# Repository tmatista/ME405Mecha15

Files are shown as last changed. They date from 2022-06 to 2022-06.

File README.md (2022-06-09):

# ME 405 Mechatronics Pen Plotter Landing Page
#### Authors: Tim Matista, Jason Hu
#### Under the Guidance of: Professor Charlie Refvem, Cal Poly SLO
#### Date: 06/04/2022

## The Pen Plotter Project Definition
#### The Pen Plotter project was devised to allow teams to create a robotic drawing machine in any creative was possible. The requirements for this project were to create a 2-and-a-half degree of freedom robot that, when fed raw HPGL files, draws out shapes using any means necessary. The term "draw" was free to be interpreted in whatever manner we choose. The two main degrees of freedom are as well free to be chosen to be any motion EXCEPT the cartesian coordinate system. The remaining half degree of freedom is used as an actuator, or pen-up pen-down motion. 
#### All devices also must be able to be ran using benchtop power supplies in the laboratory and include a "Bell and Whistle" to uniquely define this project from any similar project done before. 

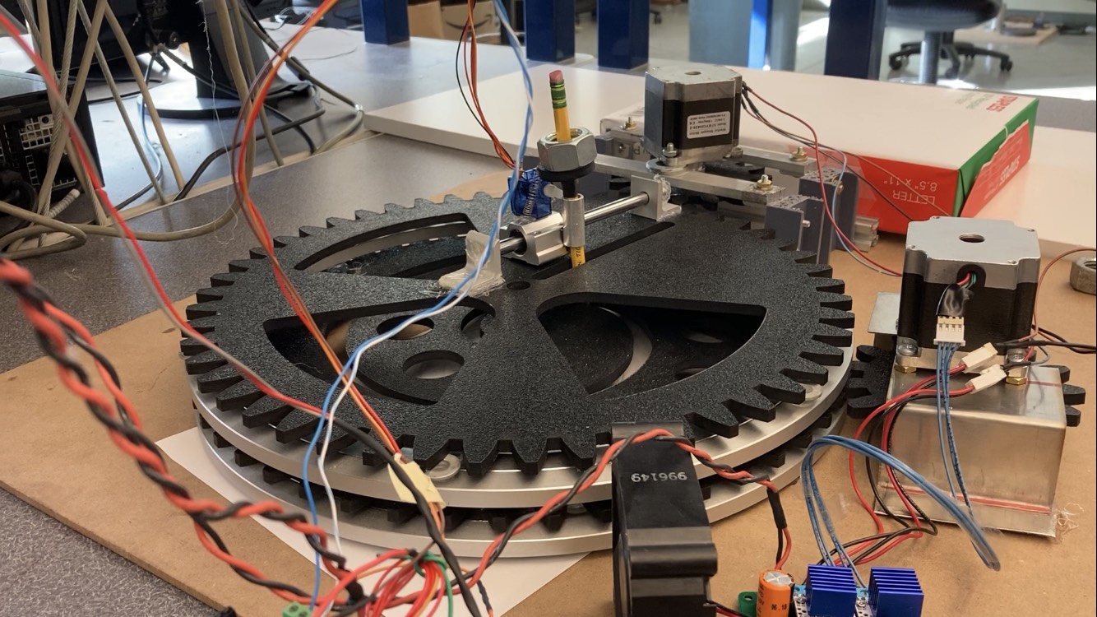
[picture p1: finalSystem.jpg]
Image of assembled System


## Features
#### Our pen plotter design offers a large workspace and the radial symmetry of the system lends itself well to geometric patterened drawings. The pen plotter can raise and lower the pen to allow fo seperate shapes to be drawn. (WHAT ELSE ARE FEATURES?)

## Bell-and-Whistle: Live Plotting
#### The additional feature added to our system is a live plotting system that uses UART to communicate drawing progress from the Nucleo to the computer. This requires a cable to be connected to the STLink in addition to the one plugged into the Shoe of Brian. To set up the live plotting, type "pip install panda" into the command prompt to download the necessary software. Then, run the plotting file by seelcting the appropriate directory and then commanding "python uart_draw.py". A window should open and display the curent pathing of the pen plotter. (INSERT VIDEO OF UART (already uploaded) WHEN THIS IS A "PAGES")

## Operation (WE NEED A WIRING DIAGRAM FOR EVERYTING, INCLUDING SERVO AND ALL THAT)
#### To run the systme, start by saving a drawing as "simple.hpgl" to the Nucleo. Next, move the motors so that the gears are **not** meshed with the disks. This is important because the motors automatically move to their "home" position which may not be what you expect it to be. Next, ensure that the pen is in the raised position. If it isn't this can be manually adjusted by running the "simple.py". Slide a piece of paper under the disks, switch on both power supplies and soft reboot the Nucleo by pressing ctrl+D. The code will report when it has finished parsing your drawing into usable code and the motors may start moving to their home location. When all of this has finished, move the gears into place to mesh with the disks, and press any key to coninue.

#### (INSERT VIDEO OF SYSTEM RUNNING WHEN THIS IS A "PAGES")

## Mecha15's Mechanical Design
#### Team Mecha15 decided to pursue a robot similar to mechanism 94 in the book, "507 Mechanical Movements". The proposed mechanism can be found here: http://507movements.com/mm_094.html
 
### The Discs
#### The proposed mechanism 94 operates using two discs, so we laser cut two discs out of HDPE that were donated by the Robotics Club at Cal Poly. The discs can be separated into a radial disc and a spiral disc. Both gears were cut to have a diameter of 14". 
### Spiral Disc
#### The spiral disc was laser cut out of HDPE at 1/4" thickness, it was designed to have an Archimedes spiral cut into it along with a 50 gear teeth on the outer diameter. Three triangular weight-saving shapes were cut into the spiral disc to cut down on inertial load and allow the user to view drawings below.
### Radial Disc
#### The radial disc was cut with a 4.75" radial slot in it to facilitate movement. This slot starts 0.75" away from the exact center of the disc. Circular weight-saving cuts were made in the radial disc to ease inertial load and allow the user to view drawings below. This disc is outfitted with a linear rail along its radial slot to help facilitate the motion of the pen as well as keep it upright. 
### Lazy Susans
#### Two 14" Lazy Susans (LS) were purchased from Amazon at about 17$/each. These LS are mounted between both discs to facilitate the independent movement of the discs. The discs were secured to the LS using hot glue. The LS can be found on Amazon here: https://www.amazon.com/dp/B07PW63B3Q/ref=twister_B09ZTWL4NN?_encoding=UTF8&th=1
### CAD
#### The Solidworks file used in the design of this project are included in this repository. The files corresponding to the disks and pinion gears were used to laser cut the respective parts.

#### (AT SOME POINT ADD THE JYPTER FILES AND ALL THAT KIND OF STUFF)

## The Motors
### Steppers
#### Two Wantai NEMA 23 motors were chosen for the final design, as these motors are able to produce the torque needed to move both discs independently. These motors are configures in 4-wire bi-polar stepper movement and have 200 counts-per-revolution. These motors are mounted on brackets to elevate them to the desired height. Pinion gears with 15 teeth are attached to the output shafts of the motor and are designed to mesh with the radial and spiral discs gear teeth. 
### Servo
#### A single TowerPro hobby servo motor was selected to control the pen actuation. The motor was dissected and altered for manual control of the internal DC motor and potentiometer. The resistance of the potentiometer changes as the motor spins, and the reistsnace changes the reading of an ADC on the Nucleo. The servo is outfitted with a single cam on its output shaft that physically moves a pen up and down. All of this together allows the Nucleo to sense if the pen has successfuly been raised or lowered.

## The Drivers
#### Both NEMA 23 motors are driven using TMC4210 and TMC2208 driver chips. These chips were selected due to their SPI protocol and silentstepper modes of movement. These chips, along with a capacitor and header pins, were soldered to a prototyping board supplied by Charlie. This board then interfaces with the Shoe-Of-Brian mounted beneath the STM32 Nucleo Microcontroller. An exact pin-out description is as follows: 

| Motor Driver| Nucleo |
|---|---|
| EN1 | C3 |
| EN2 | C2 |
| CLK | C7 | 
| nCS1 | C0 |
| nCS2 | C4 |
| SCK | B3 |
| MOSI | MOSI2 |
| MISO | MISO2 |

## Firmware
#### The software used to impliment the robot was written in Python, for its under-the-hood libaries make calculations, matrix operations and motor movement fairly easy. The software is split up into (??6??) files: (CHECK THIS NUMBER, ADD DESCRIPTIONS FOR ALL)
#### main.py
#### task_motor.py
#### newtonraphson.py
#### tmc4210driver.py
#### filereader.py
#### ihm04a1Driver.py
#### task_share.py
#### cotask.py

### filereader.py
#### This file takes in a raw .hpgl file, parses it, then saves each X, Y, and command coordinate to a .txt file. The command coordinate is simply either a 0 or a 1 corresponding to pen up/pen down respectively. This is done by seperating the .hpgl file at every semicolon, denoting different operations, and then by commas, denoting x and y coordinates. This file will also determine if the distance between two points is greater than a set threshold and interpolates between points as needed. This file will also determine if the requested point is within the workspace that the plotter can reach and adjust points if they are not possible to draw. This file runs as a pre-processing procedure before the coooperative multitasking begins.

### tmc4210driver.py
#### This file is used to instantiate the TMC4210 chip for motor control. It also defines any methods that are used by the task_motor file such as SPI.send_recv, bytearray decoders, or bytearray translators. This allows us to communicate with the chips and access all of the associated functionality. (EXPLAIN WHAT THE METHODS ACTUALLY DO)

### ihm04a1Driver.py
#### (Explain what this does)

### task_motor.py
#### This file initiates each motor object by sending the correct byte arrays to their respective registers, setting the values of P_MUL, P_DIV, A_MAX, pulse_div, and ramp_div. A table containing these parameters is listed below. To briefly summarize, the constants we selected were chosen because of the high inertia of our mechanical system. The relatively low acceleration, for example, ensures that the motors have enough torque to spin without skipping steps. These values were calculated using (INSERT EXCEL HERE) and there is more information about them there as well. 
|  Variable  | Value |
|---|---|
| A_MAX | 80 |
| pulse_div  | 10 |
| ramp_div | 8 |
| P_MUL | 156 |
| P_DIV | 3 |

### newtonraphson.py
#### The Newton Raphson file uses the Newton Raphson method of finding the roots of a non-linear equation to converge on values of theta for the motors. This is how we calculate the inverse kinematics for the system, letting us find the appropriate motor locations to move the pen to a target point.Hand calculations of the Newton Raphson process are attached below.

( Image of assembled System ) (CHANGE THIS TO MATCH IMAGE NAMES FOR HAND CALCS)

### main.py
#### The main file is responsible for scheduling and instantiating the tasks that run all the files described above. We opted with a round-robin scheduling instead of a priority scheduling technique to make sure each task had the opportunity to run. The scheduling for the running of each task is outlined in the table below. The motor task sends the desired position to each motor and them checks if the motors have reached that position. Note that the equation_task and theta_task run at the same period and priority. This would nomrally be a problem, but only one of these tasks can run at a time. These tasks are in chage of determining desired motor positions from either a .hpgl or from a mathmatical pattern, respecitvely. The pud_driver task is in chage fof raising and lowering the pen throughout the drawing process.

| Task Name |  Period (ms) | Priority |
| --- | --- | --- |
| motor_task | 75 | 0 |
| theta_task | 75 | 1 |
| equation_task | 75 | 1 |
| pud_driver | 50 | 2 |

## Difficulties
### Software
#### Many issues faced while coding this project can be attributed to an error found in the creation of the serial bus used to communicate with the TMC4210 chips. The baudrate of this connection was mistakenly set as 100,000 rather than 1,000,000. Once this issue was addressed, the motors worked much more consistantly.
### Hardware(FILL IN THE BLANKS HERE)
#### This project was fraught with hardware difficulties, most stemming from the motors used for the project. Firstly, the provided (part number) motors did not have the torque required to spin the lazy susan bearings. These motors were replaced with (part number) NEMA (number) stepper motors from the Cal Poly Robotics Club. Unfortunately, one of these replacement motors has a shorting problem when the wires are moved. With much difficulty, this has successfuly been mitigated.

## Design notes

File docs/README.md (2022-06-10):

# ME 405 Mechatronics Pen Plotter Landing Page
#### Authors: Tim Matista, Jason Hu
#### Under the Guidance of: Professor Charlie Refvem, Cal Poly SLO
#### Date: 06/04/2022

## The Pen Plotter Project Definition
#### The Pen Plotter project was devised to allow teams to create a robotic drawing machine in any creative was possible. The requirements for this project were to create a 2-and-a-half degree of freedom robot that, when fed raw HPGL files, draws out shapes using any means necessary. The term "draw" was free to be interpreted in whatever manner we choose. The two main degrees of freedom are as well free to be chosen to be any motion EXCEPT the cartesian coordinate system. The remaining half degree of freedom is used as an actuator, or pen-up pen-down motion. 
#### All devices also must be able to be ran using benchtop power supplies in the laboratory and include a "Bell and Whistle" to uniquely define this project from any similar project done before. 

Image of assembled System

## Features
#### Our pen plotter design offers a large workspace and the radial symmetry of the system lends itself well to geometric patterened drawings. The pen plotter can raise and lower the pen to allow fo seperate shapes to be drawn.

## Bell-and-Whistle: Live Plotting
#### The additional feature added to our system is a live plotting system that uses UART to communicate drawing progress from the Nucleo to the computer. This requires a cable to be connected to the STLink in addition to the one plugged into the Shoe of Brian. To set up the live plotting, type "pip install panda" into the command prompt to download the necessary software. Then, run the plotting file by seelcting the appropriate directory and then commanding "python uart_draw.py". A window should open and display the curent pathing of the pen plotter. 

(http://www.youtube.com/watch?v=P3Ct4gNFd5c)

## Operation
#### To run the systme, start by saving a drawing as "simple.hpgl" to the Nucleo. Next, move the motors so that the gears are **not** meshed with the disks. This is important because the motors automatically move to their "home" position which may not be what you expect it to be. Next, ensure that the pen is in the raised position. If it isn't this can be manually adjusted by running the "simple.py". Slide a piece of paper under the disks, switch on both power supplies and soft reboot the Nucleo by pressing ctrl+D. The code will report when it has finished parsing your drawing into usable code and the motors may start moving to their home location. When all of this has finished, move the gears into place to mesh with the disks, and press any key to coninue.

(http://www.youtube.com/watch?v=kh2zqIlsFNg)

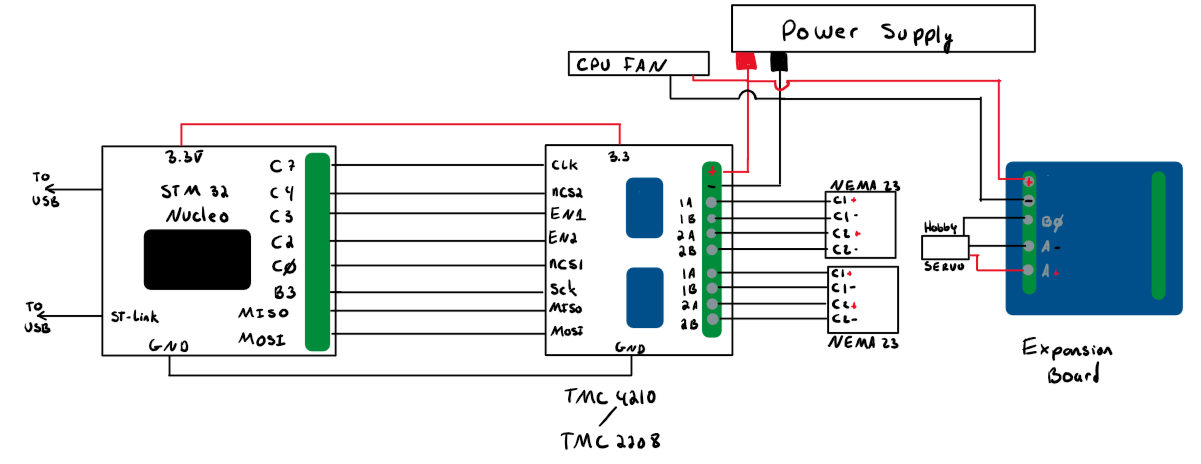
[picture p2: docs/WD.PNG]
Wiring Diagram

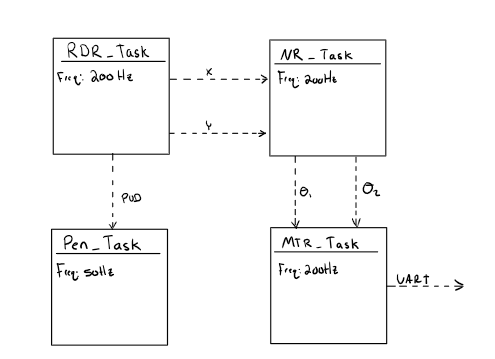
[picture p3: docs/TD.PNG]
High-Level Task Diagram


## Mecha15's Mechanical Design
#### Team Mecha15 decided to pursue a robot similar to mechanism 94 in the book, "507 Mechanical Movements". The proposed mechanism can be found here: http://507movements.com/mm_094.html
### The Discs
#### The proposed mechanism 94 operates using two discs, so we laser cut two discs out of HDPE that were donated by the Robotics Club at Cal Poly. The discs can be separated into a radial disc and a spiral disc. Both gears were cut to have a diameter of 14". 
### Spiral Disc
#### The spiral disc was laser cut out of HDPE at 1/4" thickness, it was designed to have an Archimedes spiral cut into it along with a 50 gear teeth on the outer diameter. Three triangular weight-saving shapes were cut into the spiral disc to cut down on inertial load and allow the user to view drawings below.
### Radial Disc
#### The radial disc was cut with a 4.75" radial slot in it to facilitate movement. This slot starts 0.75" away from the exact center of the disc. Circular weight-saving cuts were made in the radial disc to ease inertial load and allow the user to view drawings below. This disc is outfitted with a linear rail along its radial slot to help facilitate the motion of the pen as well as keep it upright. 
### Lazy Susans
#### Two 14" Lazy Susans (LS) were purchased from Amazon at about 17$/each. These LS are mounted between both discs to facilitate the independent movement of the discs. The discs were secured to the LS using hot glue. The LS can be found on Amazon here: https://www.amazon.com/dp/B07PW63B3Q/ref=twister_B09ZTWL4NN?_encoding=UTF8&th=1
### CAD
#### The Solidworks file used in the design of this project are included in this repository. The files corresponding to the disks and pinion gears were used to laser cut the respective parts.

## The Motors
### Steppers
#### Two Wantai NEMA 23 motors were chosen for the final design, as these motors are able to produce the torque needed to move both discs independently. These motors are configures in 4-wire bi-polar stepper movement and have 200 counts-per-revolution. These motors are mounted on brackets to elevate them to the desired height. Pinion gears with 15 teeth are attached to the output shafts of the motor and are designed to mesh with the radial and spiral discs gear teeth. 
### Servo
#### A single TowerPro hobby servo motor was selected to control the pen actuation. The motor was dissected and altered for manual control of the internal DC motor and potentiometer. The resistance of the potentiometer changes as the motor spins, and the reistsnace changes the reading of an ADC on the Nucleo. The servo is outfitted with a single cam on its output shaft that physically moves a pen up and down. All of this together allows the Nucleo to sense if the pen has successfuly been raised or lowered.

## The Drivers
#### Both NEMA 23 motors are driven using TMC4210 and TMC2208 driver chips. These chips were selected due to their SPI protocol and silentstepper modes of movement. These chips, along with a capacitor and header pins, were soldered to a prototyping board supplied by Charlie. This board then interfaces with the Shoe-Of-Brian mounted beneath the STM32 Nucleo Microcontroller. An exact pin-out description is as follows: 

| Motor Driver| Nucleo |
|---|---|
| EN1 | C3 |
| EN2 | C2 |
| CLK | C7 | 
| nCS1 | C0 |
| nCS2 | C4 |
| SCK | B3 |
| MOSI | MOSI2 |
| MISO | MISO2 |

## Firmware
#### The software used to impliment the robot was written in Python, for its under-the-hood libaries make calculations, matrix operations and motor movement fairly easy. The software is split up into 10 files:
#### main.py
#### task_motor.py
#### newtonraphson.py
#### tmc4210driver.py
#### filereader.py
#### ihm04a1Driver.py
#### uart_draw.py
#### uarter.py
#### task_share.py
#### cotask.py

### main.py
#### The main file is responsible for scheduling and instantiating the tasks that run all the files described above. We opted with a round-robin scheduling instead of a priority scheduling technique to make sure each task had the opportunity to run. The scheduling for the running of each task is outlined in the table below. The motor task sends the desired position to each motor and them checks if the motors have reached that position. Note that the equation_task and theta_task run at the same period and priority. This would nomrally be a problem, but only one of these tasks can run at a time. These tasks are in chage of determining desired motor positions from either a .hpgl or from a mathmatical pattern, respecitvely. The pud_driver task is in chage fof raising and lowering the pen throughout the drawing process.

| Task Name |  Period (ms) | Priority |
| --- | --- | --- |
| motor_task | 75 | 0 |
| theta_task | 75 | 1 |
| equation_task | 75 | 1 |
| pud_driver | 50 | 2 |

### filereader.py
#### This file takes in a raw .hpgl file, parses it, then saves each X, Y, and command coordinate to a .txt file. The command coordinate is simply either a 0 or a 1 corresponding to pen up/pen down respectively. This is done by seperating the .hpgl file at every semicolon, denoting different operations, and then by commas, denoting x and y coordinates. This file will also determine if the distance between two points is greater than a set threshold and interpolates between points as needed. This file will also determine if the requested point is within the workspace that the plotter can reach and adjust points if they are not possible to draw. This file runs as a pre-processing procedure before the coooperative multitasking begins.

### task_motor.py
#### This file initiates each motor object by sending the correct byte arrays to their respective registers, setting the values of P_MUL, P_DIV, A_MAX, pulse_div, and ramp_div. A table containing these parameters is listed below. To briefly summarize, the constants we selected were chosen because of the high inertia of our mechanical system. The relatively low acceleration, for example, ensures that the motors have enough torque to spin without skipping steps. These values were calculated using the linked Excel sheet by Trinamic and there is more information about them there as well. https://www.trinamic.com/fileadmin/assets/Products/ICs_Documents/tmc429_ramp_setup.xls

|  Variable  | Value |
|---|---|
| A_MAX | 80 |
| pulse_div  | 10 |
| ramp_div | 8 |
| P_MUL | 156 |
| P_DIV | 3 |

### newtonraphson.py
#### The Newton Raphson file uses the Newton Raphson method of finding the roots of a non-linear equation to converge on values of theta for the motors. This is how we calculate the inverse kinematics for the system, letting us find the appropriate motor locations to move the pen to a target point. Hand calculations of the Newton Raphson process are attached below, as well as a gif of a simulated drawing in action.

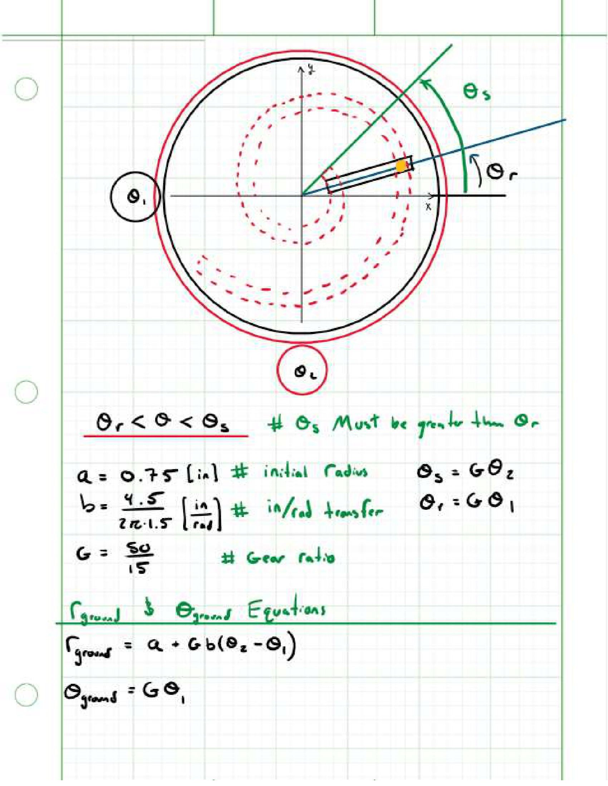
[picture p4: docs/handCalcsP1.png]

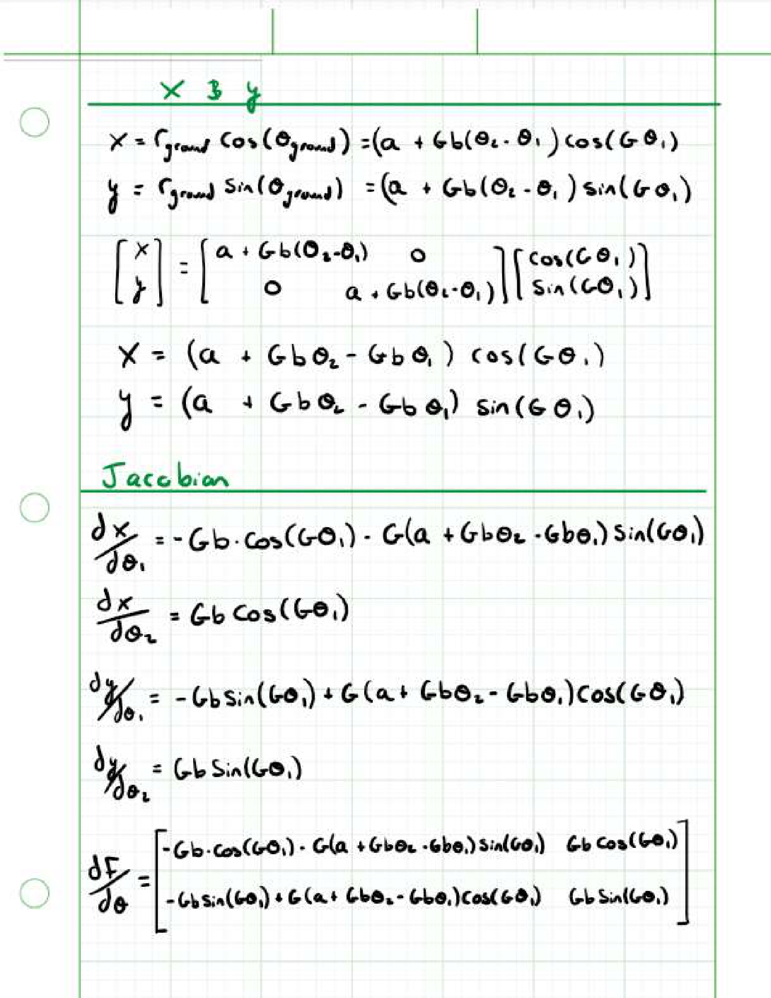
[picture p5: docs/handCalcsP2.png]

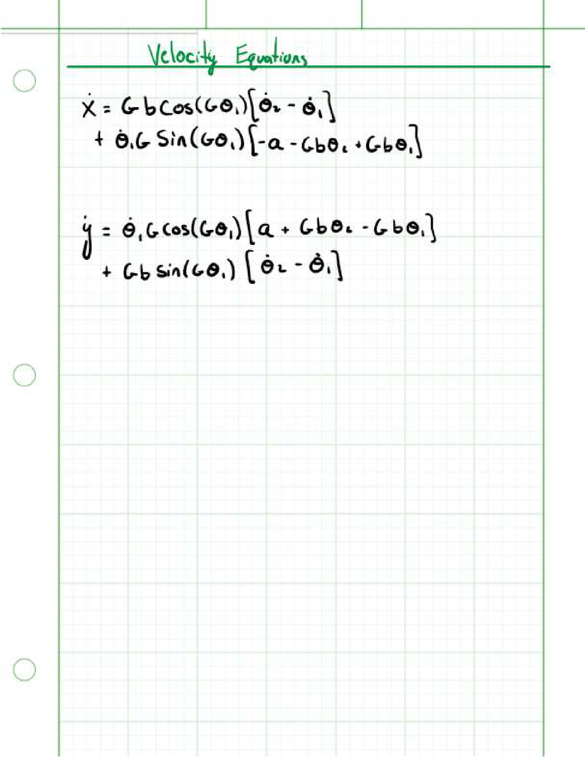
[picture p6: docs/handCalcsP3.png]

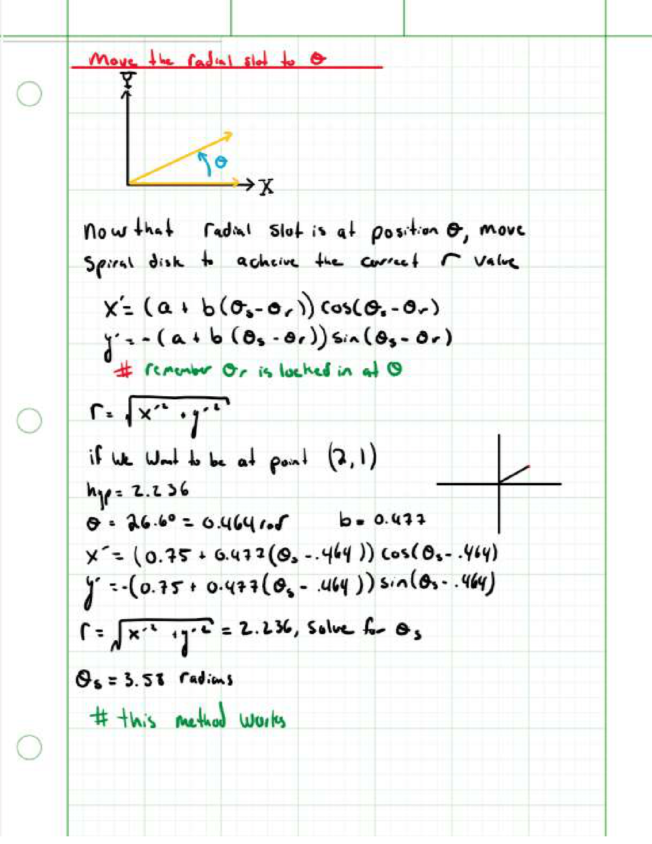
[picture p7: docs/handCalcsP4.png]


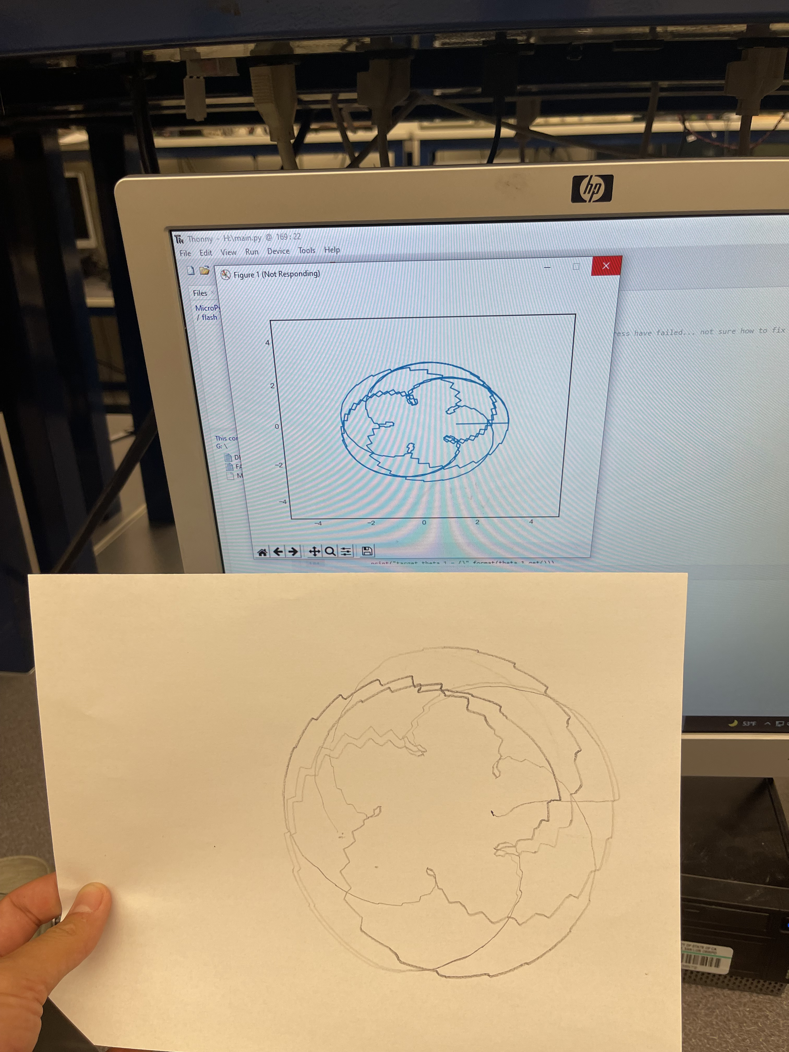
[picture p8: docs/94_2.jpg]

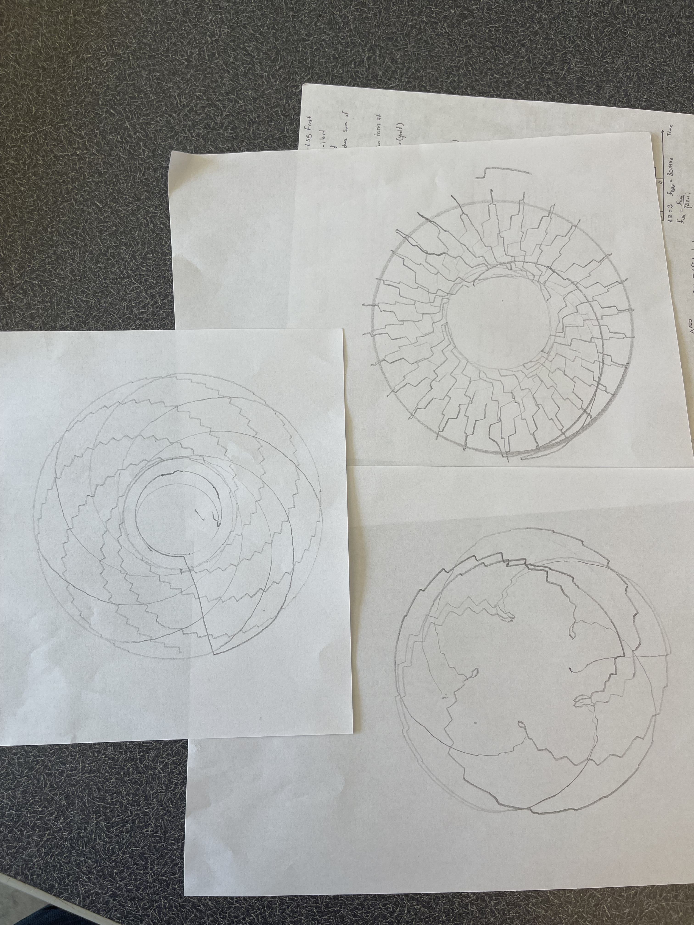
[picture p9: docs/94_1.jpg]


### tmc4210driver.py
#### This file is used to instantiate the TMC4210 chip for motor control. It also defines any methods that are used by the task_motor file such as SPI.send_recv, bytearray decoders, or bytearray translators. This allows us to communicate with the chips and access all of the associated functionality.

### ihm04a1Driver.py
#### This file allows for control of the IHM04A1 motor driver board which controls the servo. See above for more information on the servo control.

### uart_draw.py and uarter.py
#### These files facilitate the sending and recieving of drawing progress between the Nucleo and the computer using UART protocol. This is our "bell and whistle" for this project.

### Provided code
#### Both cotask.py and task_share.py were prided for this project. task_share.py creates the Share and Queue classes which are very useful for sharing variables between tasks. cotask.py drives the cooperative multitasking that is central to the project. 

## Difficulties
### Software
#### Many issues faced while coding this project can be attributed to an error found in the creation of the serial bus used to communicate with the TMC4210 chips. The baudrate of this connection was mistakenly set as 100,000 rather than 1,000,000. Once this issue was addressed, the motors worked much more consistantly.
### Hardware
#### This project was fraught with hardware difficulties, most stemming from the motors used for the project. Firstly, the provided stepper motors did not have the torque required to spin the lazy susan bearings. These motors were replaced with NEMA 23 stepper motors from the Cal Poly Robotics Club. Unfortunately, one of these replacement motors has a shorting problem when the wires are moved. With much difficulty, this has successfuly been mitigated.

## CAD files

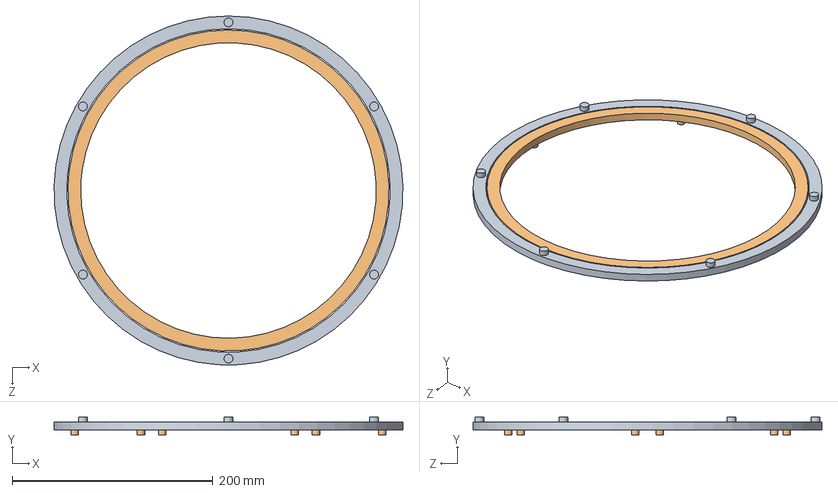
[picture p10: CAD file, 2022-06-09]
lazySusan.SLDASM
347.8 x 17.8 x 348.0 mm
outerRing^lazySusan
innerRing^lazySusan

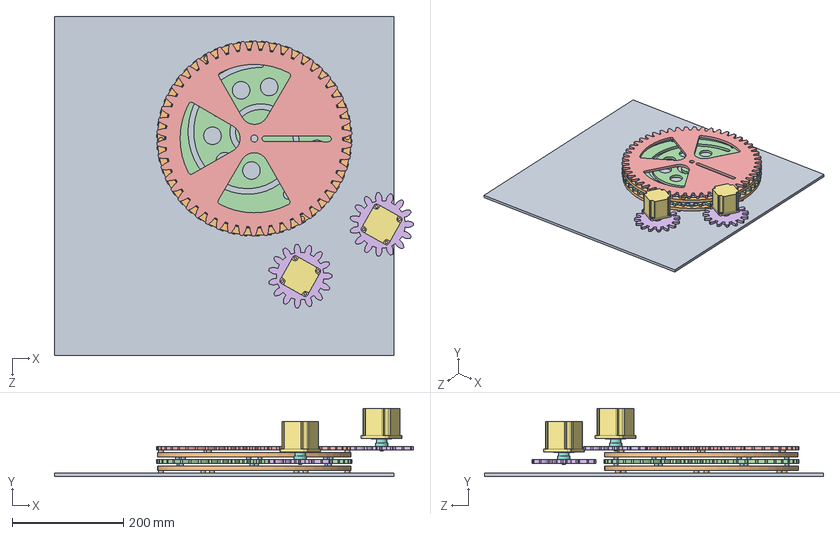
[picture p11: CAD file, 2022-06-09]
405TermProject.SLDASM
645.0 x 122.9 x 609.6 mm
outerRing^lazySusan x 2
innerRing^lazySusan x 2
spiralGear
radialGear
15tooth x 2
NEMA23 x 2
hub^405TermProject x 2

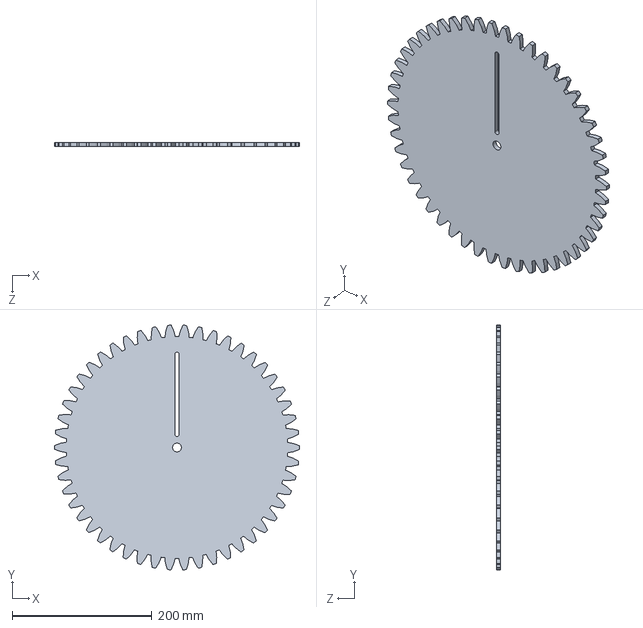
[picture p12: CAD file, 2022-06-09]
radialGear.SLDPRT
350.9 x 350.6 x 6.35 mm

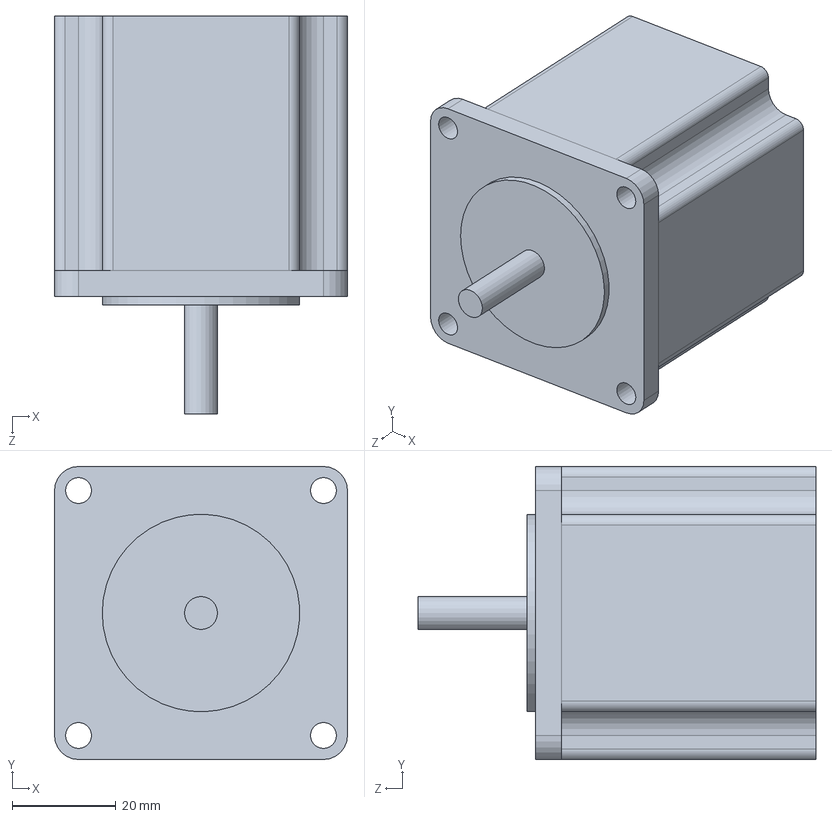
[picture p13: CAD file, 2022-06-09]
NEMA23.SLDPRT
56.4 x 56.4 x 76.6 mm

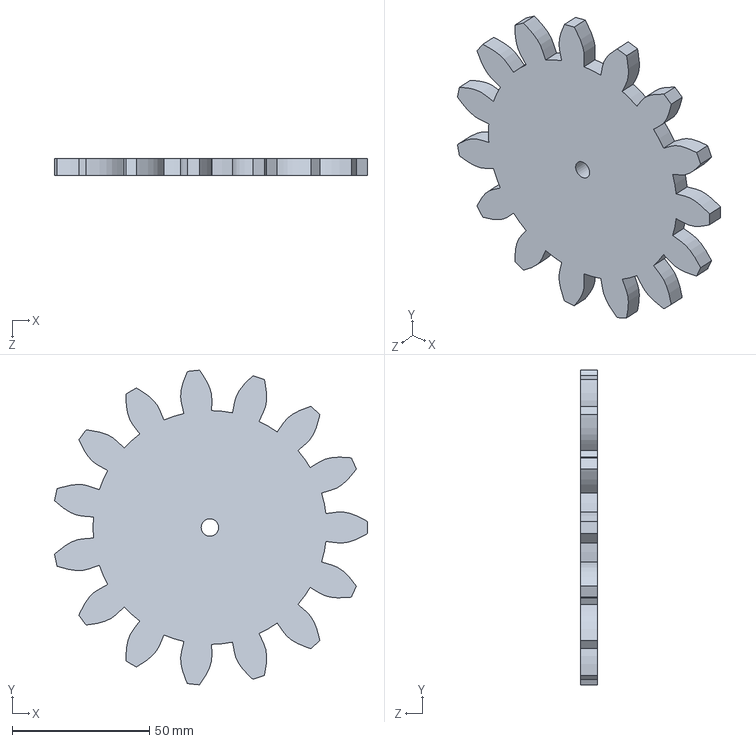
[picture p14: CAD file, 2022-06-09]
15tooth.SLDPRT
113.9 x 114.5 x 6.35 mm

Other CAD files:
spiralGear.SLDPRT

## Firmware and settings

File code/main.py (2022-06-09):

import cotask
import task_share
import task_motor
import newtonraphson
import filereader
import ihm04a1Driver
from pyb import UART, repl_uart
import utime
import micropython
from ulab import numpy as np
from math import pi, cos, sin
import gc


# This file will run the cotask function and control task execution
# This file will also instantiate all the shared variables that we need. Like theta.


# These are shares made for the bell and whistle. 
actx = task_share.Share('f', thread_protect = True)
acty = task_share.Share('f', thread_protect = True)

# X is the desired X coordinate
x = task_share.Share('f', thread_protect = True)

# Y is the desired Y coordinate
y = task_share.Share('f', thread_protect = True)

# Theta_1 will control the RADIAL DISK
theta_1 = task_share.Share('f', thread_protect = True)

#Theta_2 will control the SPIRAL DISK
theta_2 = task_share.Share('f', thread_protect = True)

# PUD is the pen up/down flag
pud = task_share.Share('f', thread_protect = True)
pud.put(0.0)

# First things first, Take the inkscape hpgl file and parse it into a new file
# filename = "simple.hpgl"
# filename = "drawing.hpgl"
# filename = "single target point.hpgl"
# filename = "bigdiamond.hpgl"
filename = "timTest.hpgl"
fr = filereader.Drawer()
fr.Draw(filename)

#arrive flag, denots if motors have arrived at target location. Prevent other tasks from running again until set 1
ar_flag = task_share.Share('d', thread_protect = True) #check format instead of float use bool
ar_flag.put(1)

driver = task_motor.Motor_Driver()
driver.Motor_Runner(0,0)
hello = input('Are you ready to continue?')

# Uart initialization
repl_uart(None)
uart = UART(2,115200)
uart.init(115200, 8, 0, 1)

# def start_program():
#     repl_uart(None)
#     uart = UART(2,115200)
#     uart.init(115200, 8, 0, 1)
#     motor_driver = task_motor.Motor_Driver()
#     motor_driver.Motor_Runner(0,0)
#     hello = input('Are you ready to continue?')
#     return 

def Motor_Drv():  
    driver = task_motor.Motor_Driver() #we might be able to get rid of this line since we have alread init the motor driver
    theta1 = theta_1.get()
    theta2 = theta_2.get()
    driver.Motor_Runner(theta1, theta2)
    
    while True:
        th1, th2 = driver.get_actual()
        uart.write(f'{th1} : {th2} \n')
        if ar_flag.get() == 0: #if ar_flag is False we are not at target location so run motors
            theta1 = theta_1.get()
            theta2 = theta_2.get()
            driver.Motor_Runner(theta1, theta2)
            ar_flag.put(driver.at_target(theta1, theta2)) #update bool in ar_flag based on at_target()
            
        if ar_flag.get() == 1:
            print('motors have arrived at target location')
        yield None   
        
        
def Pen_Drv():
    servo_drv     = ihm04a1Driver.ihm04a1()
    servo_1       = servo_drv.servo(1)
    servo_drv.enable()
    while True:
        if pud.get() == 1:
            servo_1.pd()
        if pud.get() == 0:
            servo_1.pu()
        yield None

    
def get_Thetas(): #gives error on last line (blank) and attempts to address have failed... not sure how to fix but since its last line no biggie?
    raphson = newtonraphson.NewtRaph()
    theta_guess = np.array([[0],[0]])
    xyfile = open('xy.txt', 'r')
    while True:
        
        if ar_flag.get() ==0:
            yield None
        
        if ar_flag.get() == 1:
            ar_flag.put(0)
            print('generating new thetas')
            line = xyfile.readline()

            print("line: {}".format(line))
            xy_coords = line.split(',')
            
            if xy_coords[0] == '':
                print('blank')
                break
            
            x_des = float(xy_coords[0])
            y_des = float(xy_coords[1])
            ud = int(xy_coords[2])
            pud.put(ud)
            
            x_desired = np.array([ [x_des],[y_des] ])
 
             # NR outputs the value in RADIANS, this must turn to degrees
            thetas = raphson.Raphson_Runner(x_desired, theta_guess)

            theta_guess[0][0] = thetas[0][0]    #this pinion in radians
            theta_guess[1][0] = thetas[1][0]

            # Motor angles are converted to degrees here  
            theta_1.put(180*thetas[0][0]/(pi))
            theta_2.put(180*thetas[1][0]/(pi))
            
            print("target theta 1 = {}".format(theta_1.get()))
            print("target theta 2 = {}".format(theta_2.get()))
            yield None
        print('done')    


def equation_drive(): #gives error on last line (blank) and attempts to address have failed... not sure how to fix but since its last line no biggie?
    raphson = newtonraphson.NewtRaph()
    theta_guess = np.array([[0],[0]])
    c = 0
    circle = np.linspace(6,2292,382)
    offset = np.array([[2],[2]])
    while True:
        if ar_flag.get() == 0:
            yield None
            
        if ar_flag.get() == 1:
            print('Generating New Thetas')
            ar_flag.put(0)
            x_des = 1*cos(0.15*c)*offset[0][0] + cos(circle[c])
            y_des = 1*sin(0.15*c)*offset[1][0] + sin(circle[c])
            x_desired = np.array([ [x_des],[y_des] ])
            c += 1
            print(c)
            print(x_des, y_des)
            # NR outputs the value in RADIANS, this must turn to degrees
            thetas = raphson.Raphson_Runner(x_desired, theta_guess)
            
            
            theta_guess[0][0] = thetas[0][0]    #this pinion in radians
            theta_guess[1][0] = thetas[1][0]

            # Motor angles are converted to degrees here  
            theta_1.put(180*(thetas[0][0] + 6*2*pi)/(pi))
            theta_2.put(180*(thetas[1][0] + 6*2*pi)/(pi))
            
            print("target theta 1 = {}".format(theta_1.get()))
            print("target theta 2 = {}".format(theta_2.get()))
            yield None
    print('done')    
            
        
motor_task = cotask.Task(Motor_Drv, 'function_1', priority=0, period=75, profile=True, trace=True)
cotask.task_list.append(motor_task)

theta_task = cotask.Task(get_Thetas, 'function_2', priority=1, period=75, profile=True, trace=True)
cotask.task_list.append(theta_task)


# equation_task = cotask.Task(equation_drive, 'function_2', priority = 1, period = 200, profile = True, trace = True)
# cotask.task_list.append(equation_task)

pud_driver = cotask.Task(Pen_Drv, 'function_4', priority=2, period=50, profile=True, trace=True)
cotask.task_list.append(pud_driver)


while True:
    cotask.task_list.rr_sched()

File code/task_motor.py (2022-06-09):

import pyb
from pyb import Timer, SPI, delay
import tmc4210drv

#Class Motor_Driver:
class Motor_Driver():
    def __init__(self):
        #timer and clock inputs
        self.AR = 2 #auto reload value (aka period)
        self.tim_num = 4 #timer number
        self.ch_num = 2
        self.compVal = 2 #compare value informs pulse width

        # Pin Initiation
        self.clkPin = pyb.Pin(pyb.Pin.cpu.B7, mode=pyb.Pin.OUT_PP) #SCL pin
        self.EN1 = pyb.Pin(pyb.Pin.cpu.C3, mode=pyb.Pin.OUT_PP, value=1) #EN1 pin
        self.EN2 = pyb.Pin(pyb.Pin.cpu.C2, mode=pyb.Pin.OUT_PP, value=1) # EN2 pin
        self.nCS1 = pyb.Pin(pyb.Pin.cpu.C0, mode=pyb.Pin.OUT_PP, value=1) #nCS1 Chip Select pin
        self.nCS2 = pyb.Pin(pyb.Pin.cpu.C4, mode=pyb.Pin.OUT_PP, value=1) #nCS2 Chip Select pin
        self.sck = pyb.Pin(pyb.Pin.cpu.B8, mode=pyb.Pin.OUT_PP) #sck pin

        ## PWM timers and clocks
        self.tim = pyb.Timer(self.tim_num, period = self.AR, prescaler = 0)
        self.clk = self.tim.channel(2, pin=self.clkPin, mode=Timer.PWM, pulse_width=self.compVal)

        ## ======= READ-ONLY REGISTERS======
        type_register = bytearray([0b01110011,
                                   0b00000000,
                                   0b00000000,
                                   0b00000000])

        self.x_actual1 = bytearray([0b00000011,
                              0b00000000,
                              0b00000000,
                              0b00000000])
        
        self.x_actual2 = bytearray([0b00000011,
                              0b00000000,
                              0b00000000,
                              0b00000000])

        v_actual = bytearray([0b00001011,
                              0b00000000,
                              0b00000000,
                              0b00000000])

        a_actual = bytearray([0b00001111,
                              0b00000000,
                              0b00000000,
                              0b00000000])

        ## ======= WRITE-ONLY REGISTERS======    

        self.x_target1 = bytearray([0b00000000,
                              0b00000000,
                              0b00000000,
                              0b00000000])
        
        self.x_target2 = bytearray([0b00000000,
                              0b00000000,
                              0b00000000,
                              0b00000000])

        v_min =    bytearray([0b00000100,
                              0b00000000,
                              0b00000000,
                              0b00001010])

#         v_max =    bytearray([0b00000110,
#                               0b00000000,
#                               0b00000000,
#                               0b10001010])
        
        v_max =    bytearray([0b00000110,
                              0b00000000,
                              0b00000001,
                              0b01100101]) # v_max = 357
        
        

        self.v_target1 =  bytearray([0b00001000,
                                     0b00000000,
                                     0b00000000,
                                     0b00000000])
        
        self.v_target2 =  bytearray([0b00001000,
                                     0b00000000,
                                     0b00000000,
                                     0b00000000])

        #A_max is set to 1040 (10000010000)
        # set to 200 (11001000)
        # set to 100 (0110100)
        # set to 255 (11111111)
        # Set to 2000 (11111010000)
#         a_max =   bytearray([0b000001100,
#                               0b00000000,
#                               0b00000111,
#                               0b11001000])


        a_max =   bytearray([0b000001100,
                              0b00000000,
                              0b00000000,
                              0b01010000]) #a_max = 80

        #This address sets the en_sd register to 1
        IF_configuration_4210 = bytearray([0b01101000,
                                           0b00000000,
                                           0b00000000,
                                           0b00100000])
        # ramp: 1 pulse:3
#         ([0b00011000,
#         0b00000000,
#         0b00110001,
#         0b00000000 ])
        # Pulse: 0 Ramp: 0
        # ramp: 6 pulse: 4
#         pulse_ramp_div = bytearray([0b00011000,
#                                     0b00000000,
#                                     0b01000110,
#                                     0b00000000 ])


        pulse_ramp_div = bytearray([0b00011000,
                                    0b00000000,
                                    0b10101000, #puls_div = 10 ramp_div = 8
                                    0b00000000 ])


        P_mul_div = bytearray([0b00010010,
                               0b00000000,
                               0b10011100,   #pmul = 156
                               0b00000010]) #pdiv = 3



        self.R_M_REF_conf = bytearray([0b00010100,
                                  0b00000000,
                                  0b00001100,
                                  0b00000000 ])

        self.vel_mode = bytearray([0b00010100,
                                  0b00000000,
                                  0b00001100,
                                  0b00000010 ])
        
        self.EN1.low()
        self.EN2.low()


        ## =======Function Calls=======
        ## TMC4210 object definitions
        self.TMC1 = tmc4210drv.TMC4210_driver()
        self.TMC2 = tmc4210drv.TMC4210_driver()

        a = self.TMC1.decoder(a_max)

        ## ========Motor Initialization=======
        #Send the en_sd register to 1
        self.nCS1.low()
        self.nCS2.low()
        self.TMC1.send(IF_configuration_4210)
        self.TMC2.send(IF_configuration_4210)

        #Set the V_min and V_max values to 10
        self.TMC1.send(v_min)
        self.TMC2.send(v_min)

        self.TMC1.send(v_max)
        self.TMC2.send(v_max)

        #Set the pulse_div and ramp_div register to 0, ramp_div divides the acceleration
        # parameter, pulse_div divides the velocity parameter
        self.TMC1.send(pulse_ramp_div)
        self.TMC2.send(pulse_ramp_div)

        #Set PMUL & PDIV
        self.TMC1.send(P_mul_div)
        self.TMC2.send(P_mul_div)

        #Set A_MAX
        self.TMC1.send(a_max)
        self.TMC2.send(a_max)

        #Set Ramp_MODE and REF_CONFIG
        self.TMC1.send(self.R_M_REF_conf)
        self.TMC2.send(self.R_M_REF_conf)
        self.nCS1.high()
        self.nCS2.high()
        
        
        
        #checking thresholds
        
        self.ck_thresh = 1
        

        #Homing External Interrupt
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

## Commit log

2022-06-09 Add all files
    [equationDrawing.xlsx]
2022-06-09 Create CAD Folder
2022-06-09 add CAD
    [15tooth.SLDPRT, 405TermProject.SLDASM, NEMA23.SLDPRT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]
